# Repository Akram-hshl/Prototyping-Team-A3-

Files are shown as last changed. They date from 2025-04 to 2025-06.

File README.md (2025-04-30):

# Line Follower RC Car with Obstacle Detection

This project focuses on building a smart **line-following RC car** that autonomously navigates along a track while avoiding obstacles in its path. The car uses a combination of **ultrasonic sensors**, **IR sensors**, **servo motors**, and **motor drivers** to follow a designated line and actively detect and avoid obstacles.

## Key Components:
- **IR Sensors**: Used to detect the line and keep the car on track.
- **Ultrasonic Sensor**: Detects obstacles in the car's path, enabling it to avoid collisions.
- **Servo Motors**: Control the movement of the car, ensuring smooth navigation along the line.

### Goal:
The main objective of this project is to integrate these components into a cohesive system that not only follows the line but also reacts to its environment by avoiding obstacles. This makes the project a great introduction to robotics and autonomous systems.

---

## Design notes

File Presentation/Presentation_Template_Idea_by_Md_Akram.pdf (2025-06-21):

1. Introduction and Motivation -Md Akram
2. SysML diagram (requirement, use case and activity any one or two as your wish) -Jhon
3. SysML diagram (block, state machine, sequence any one or two as your wish) -Latif
4. 3D Design & Paper Sketch -Md Akram
5. Hardware requirement (Used Components list only) and Assembly process in details -Jhon
6. Thinker Cad Simulation video and Proteus layout diagram of components pins layout -Md Akram
7. Uppaal modeling, deadlock free verification and timed behavior -Latif (please include simulation

video)

8. Programing and Implementation
- Line Following (IR Sensor, motor driver and motor details and Used algorithm for our

system. If possible add a video as a proof it functional) -Jhon

- Obstacles Detection and avoidance (Ultrasonic Sensor and servo motor in details and

Used algorithm for our system. If possible add a video as a proof it functional) -Latif or

Md Akram any one

- Color Sensor Integration for Push, avoid and parking (Color sensor details and Used

algorithm for our system. If possible add a video as a proof it functional) -Latif or Md

Akram any one

9. Implementation overview and Statistics -Md Akram
10. Conclusion and future work - Jhon

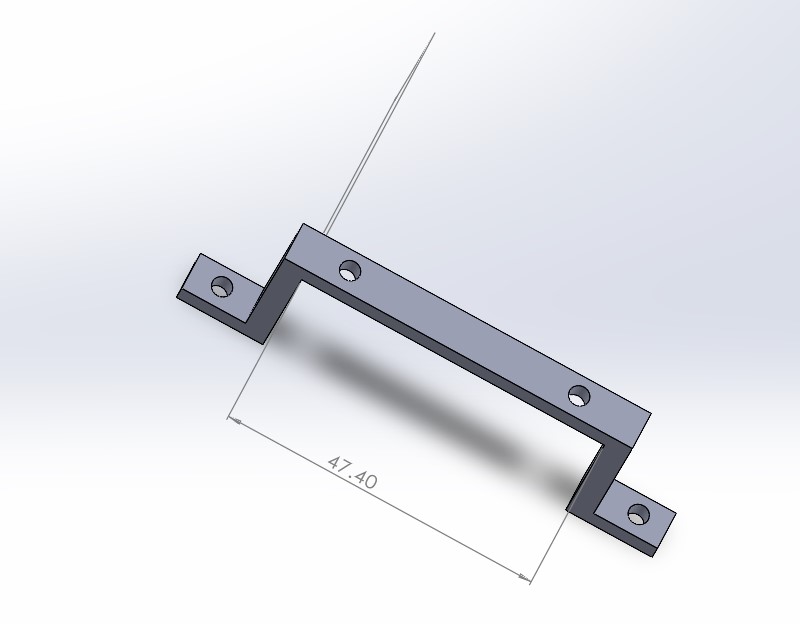
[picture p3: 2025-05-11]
Task 3 (Final Sysml, Switch case, Paper Sketch)/battery_holder.jpg

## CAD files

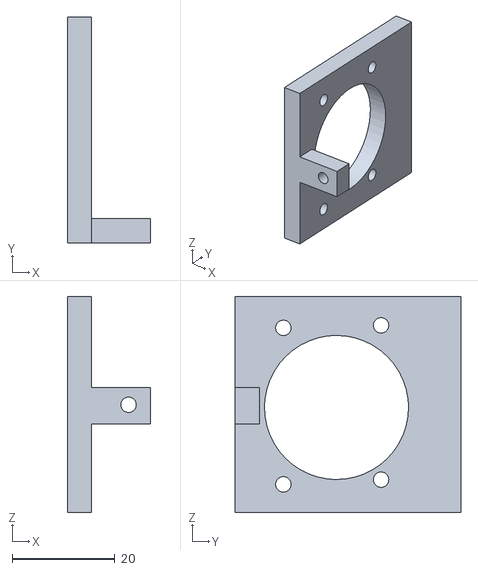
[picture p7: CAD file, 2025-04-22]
3D parts .stl format/P03_TA3_Colour_sensor_holder.STL
16.1 x 43.9 x 42.0

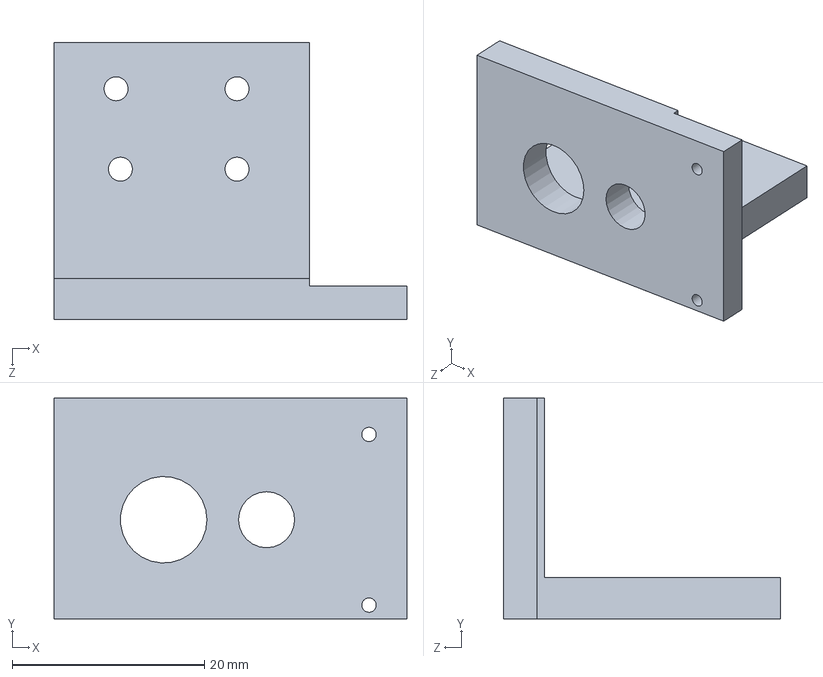
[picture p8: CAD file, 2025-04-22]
3D Parts/P05_TA3_Motor_holder_right.SLDPRT
36.7 x 23.0 x 28.8 mm

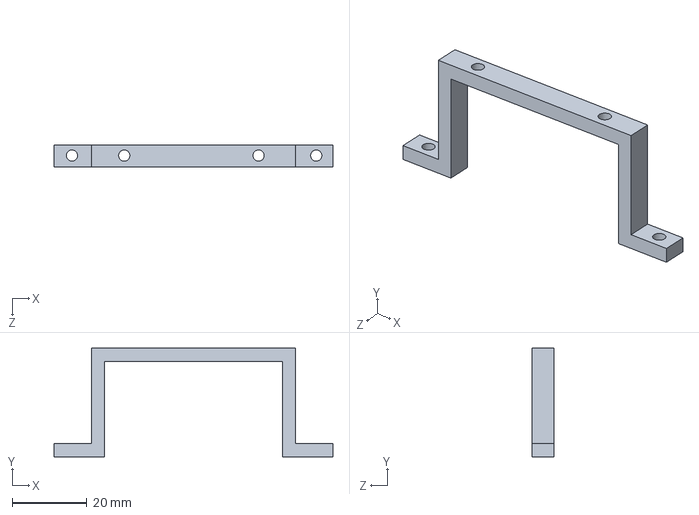
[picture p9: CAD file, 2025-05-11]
Task 3 (Final Sysml, Switch case, Paper Sketch)/P11_TA3_Battery_holder_backt side support.SLDPRT
74.5 x 29.1 x 6.00 mm

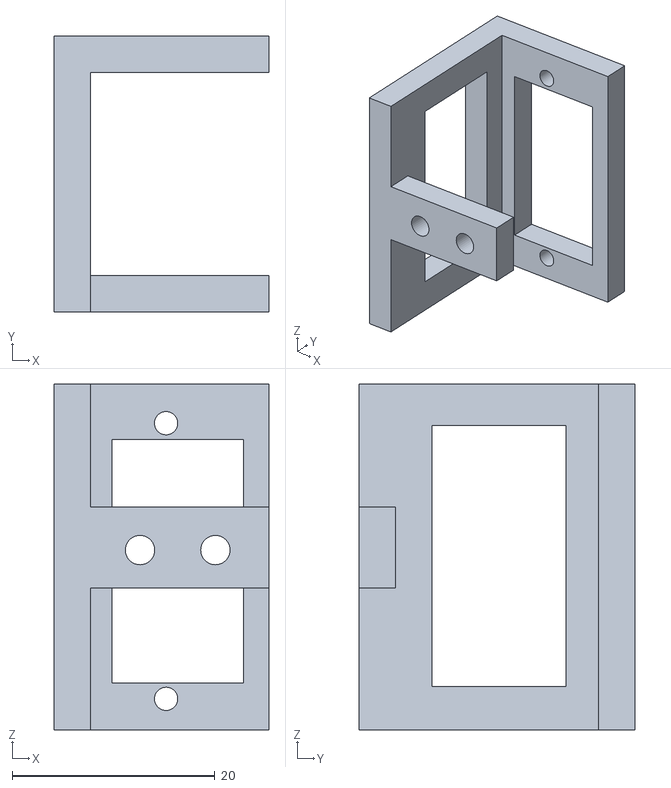
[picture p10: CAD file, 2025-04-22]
3D parts .stl format/P06_TA3_Servo_holder.STL
21.2 x 27.3 x 34.2

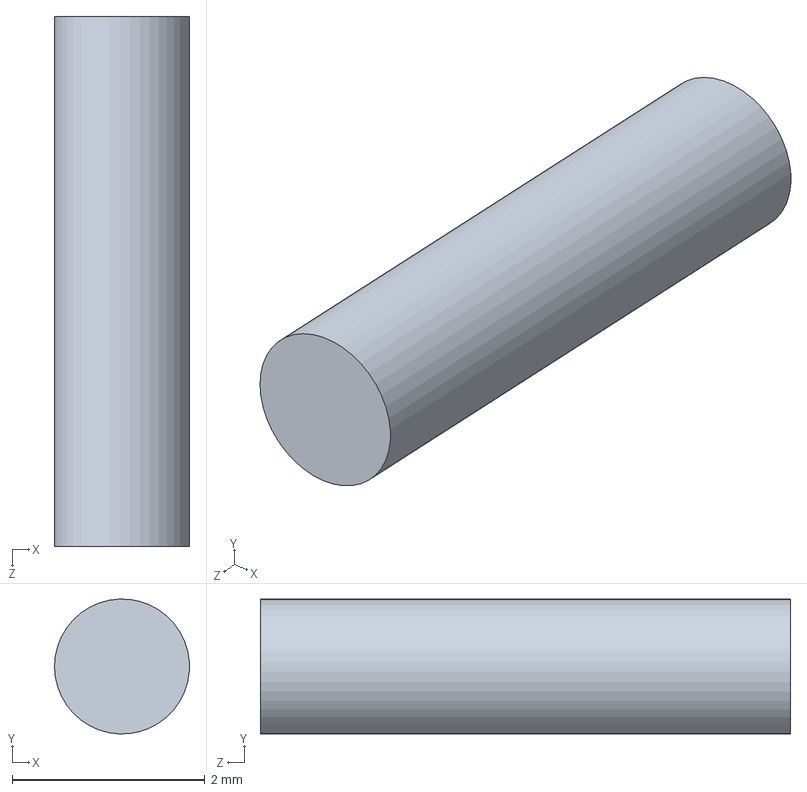
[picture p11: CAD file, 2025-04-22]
3D Parts/P08_TA3_Strick_Top.SLDPRT
1.40 x 1.40 x 5.50 mm

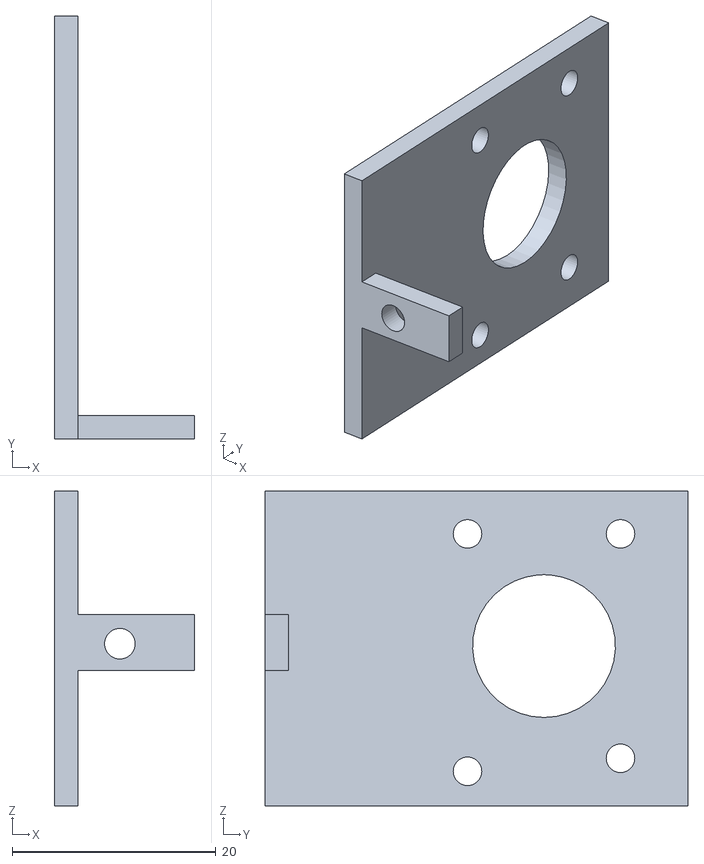
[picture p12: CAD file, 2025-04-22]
3D parts .stl format/P10_TA3_Extra_part_Pi_Camera_holder.STL
13.7 x 41.5 x 30.9

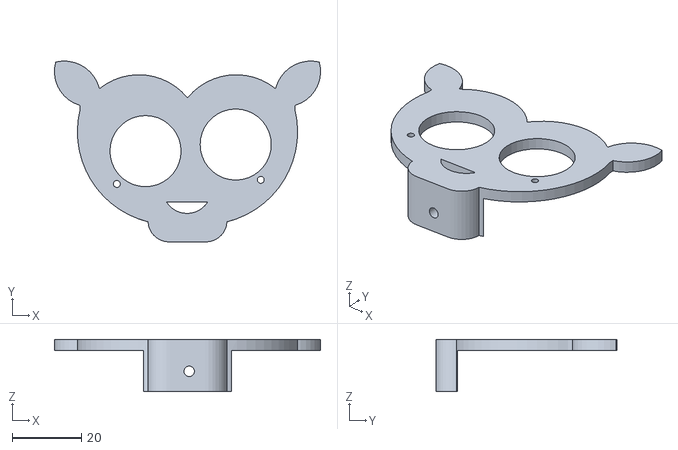
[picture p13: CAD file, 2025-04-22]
3D parts .stl format/P07_TA3_Ultrasonic_holder.STL
76.7 x 52.1 x 15.0

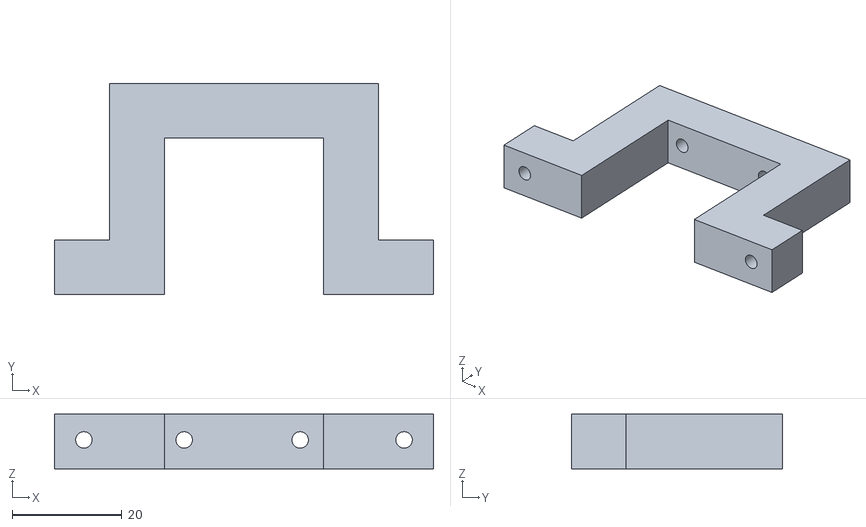
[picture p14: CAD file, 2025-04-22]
3D parts .stl format/P02_TA3_Battery_holder_front side support.STL
69.0 x 38.5 x 10.0

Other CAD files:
3D Parts/P10_TA3_Extra_part_Pi_Camera_holder.SLDPRT
3D Parts/P09_TA3_Strick_Bottom - Copy.SLDPRT
3D Parts/P07_TA3_Ultrasonic_holder.SLDPRT
3D parts .stl format/P08_TA3_Strick_Top.STL
3D Parts/P01_TA3_Battery_holder_backt side support.SLDPRT
3D parts .stl format/P05_TA3_Motor_holder_right.STL
3D Parts/P04_TA3_Motor_holder_left.SLDPRT
3D parts .stl format/P09_TA3_Strick_Bottom - Copy.STL
3D Parts/P06_TA3_Servo_holder.SLDPRT
3D parts .stl format/P04_TA3_Motor_holder_left.STL
3D Parts/P02_TA3_Battery_holder_front side support.SLDPRT
3D Parts/P03_TA3_Colour_sensor_holder.SLDPRT
3D parts .stl format/P01_TA3_Battery_holder_backt side support.STL

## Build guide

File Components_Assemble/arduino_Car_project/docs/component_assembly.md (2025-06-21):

# Component Assembly Log  
**Date:** May 11, 2025  
**Prepared by:** Onyesi John Abiagam  

## Overview  
This log records the physical setup and wiring of components for our robot during the prototyping stage. The focus was on connecting the motors, sensors, and power system properly before moving into software testing.

## Components Connected  

| Component | Connection Details |
|---|---|
| **DC Motors** | Connected to L298N motor driver: IN1–D6, IN2–D7, IN3–D8, IN4–D9. ENA on D10, ENB on D5. |
| **Ultrasonic Sensor (HC-SR04)** | Echo → A2, Trig → A3 |
| **IR Sensors (x2)** | Left sensor to A0, Right sensor to A1 |
| **Servo Motor** | Signal connected to D11, powered using external 5V |
| **Color Sensor (TCS3200)** | S0–S3 connected to D2–D5, OUT pin to D12 |
| **Power Supply** | 9V Li-ion battery to 5V voltage regulator, which powers the Arduino and sensors. All GNDs are linked. |

## What Was Done  
- All components were mounted on the chassis or breadboard.
- Double-checked wire connections for correct pins and voltage levels.
- Powered up the system and tested for signs of life (blinking LEDs, initial sensor response).
- Ran basic test code for IR sensors, ultrasonic sensor, servo, and motors to confirm they’re working.

## Notes  
- No visible signs of short circuits or heating.
- Servo works better when powered from the regulator, not directly from Arduino 5V.
- IR sensors responded correctly to black and white surfaces.
- Distance sensor gave expected readings (within ~2 cm error).
- Color sensor needs more lighting to give consistent results.

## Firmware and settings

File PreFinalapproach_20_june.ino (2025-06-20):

// Motor control pins for L298N
#define IN1 8
#define IN2 9
#define ENA 3

#define IN3 10
#define IN4 11
#define ENB 5
#define servo A5 // Servo motor control pin

// Line sensor pins
const int L_S = 2;
const int R_S = 4;

// Ultrasonic sensor pins
const int trigPin = 13;
const int echoPin = 12;

// Speed settings
const int RespeedL = 50;
const int RespeedR = 50;
const int speedL = 55;
const int speedR = 55;
const int speedLa = 75;
const int speedRa = 75;

// Obstacle detection
const int Set = 35;  

int distance_F = 0;

void setup() {
  pinMode(L_S, INPUT);
  pinMode(R_S, INPUT);

  pinMode(ENA, OUTPUT); pinMode(IN1, OUTPUT); pinMode(IN2, OUTPUT);
  pinMode(ENB, OUTPUT); pinMode(IN3, OUTPUT); pinMode(IN4, OUTPUT);

  pinMode(trigPin, OUTPUT);
  pinMode(echoPin, INPUT);
  pinMode(servo, OUTPUT);

  // Initialize servo to face forward
  servoPulse(servo, 70);
  Serial.begin(9600);
  delay(1000);
}

void loop() {
  distance_F = Ultrasonic_read();
  Serial.print("Distance Forward = ");
  Serial.print(distance_F);
  Serial.println(" cm");

  int leftSensor = digitalRead(L_S);
  int rightSensor = digitalRead(R_S);

  if ((rightSensor == 0) && (leftSensor == 0)) {
    if (distance_F > Set) {
      forward();
    } else {
      avoidObstacle();
    }
  } else if ((rightSensor == 1) && (leftSensor == 0)) {
    turnRight();
  } else if ((rightSensor == 0) && (leftSensor == 1)) {
    turnLeft();
  } else if ((rightSensor == 1) && (leftSensor == 1)) {

    Stop();
  }

  delay(10);
}
void avoidObstacle(){
  Stop();
  delay(300);
  aturnRight();
  delay(400);
  Stop();
  delay(400);
  aforward();
  delay(500);
  Stop();
  delay(200);
  aturnLeft();
  delay(400);
  Stop();
  delay(200);
  Reforward();
  delay(400);
}


int Ultrasonic_read() {
  digitalWrite(trigPin, LOW); 
  delayMicroseconds(2);
  digitalWrite(trigPin, HIGH); 
  delayMicroseconds(10);
  digitalWrite(trigPin, LOW);

  long duration = pulseIn(echoPin, HIGH, 30000);
  if (duration == 0) return 999;

  return duration / 29 / 2;
}
// Servo pulse function
void servoPulse(int pin, int angle) {
  int pwm = (angle * 11) + 500;
  digitalWrite(pin, HIGH);
  delayMicroseconds(pwm);
  digitalWrite(pin, LOW);
  delay(20);
}
// Movement functions
void forward() {
  analogWrite(ENA, speedL); analogWrite(ENB, speedR);
  digitalWrite(IN1, HIGH); digitalWrite(IN2, LOW);
  digitalWrite(IN3, HIGH); digitalWrite(IN4, LOW);
}
void Reforward() {
  analogWrite(ENA, RespeedL); analogWrite(ENB, RespeedR);
  digitalWrite(IN1, HIGH); digitalWrite(IN2, LOW);
  digitalWrite(IN3, HIGH); digitalWrite(IN4, LOW);
}
void aforward() {
  analogWrite(ENA, speedLa); analogWrite(ENB, speedRa);
  digitalWrite(IN1, HIGH); digitalWrite(IN2, LOW);
  digitalWrite(IN3, HIGH); digitalWrite(IN4, LOW);
}
void backward() {
  analogWrite(ENA, speedLa); analogWrite(ENB, speedRa);
  digitalWrite(IN1, LOW); digitalWrite(IN2, HIGH);
  digitalWrite(IN3, LOW); digitalWrite(IN4, HIGH);
}

void turnRight() {
  analogWrite(ENA, speedL); analogWrite(ENB, speedR);
  digitalWrite(IN1, LOW); digitalWrite(IN2, HIGH);
  digitalWrite(IN3, HIGH); digitalWrite(IN4, LOW);
}
void aturnRight() {
  analogWrite(ENA, speedLa); analogWrite(ENB, speedRa);
  digitalWrite(IN1, LOW); digitalWrite(IN2, HIGH);
  digitalWrite(IN3, HIGH); digitalWrite(IN4, LOW);
}

void turnLeft() {
  analogWrite(ENA, speedL); analogWrite(ENB, speedR);
  digitalWrite(IN1, HIGH); digitalWrite(IN2, LOW);
  digitalWrite(IN3, LOW); digitalWrite(IN4, HIGH);
}
void aturnLeft() {
  analogWrite(ENA, speedLa); analogWrite(ENB, speedRa);
  digitalWrite(IN1, HIGH); digitalWrite(IN2, LOW);
  digitalWrite(IN3, LOW); digitalWrite(IN4, HIGH);
}

void Stop() {
  analogWrite(ENA, 0); analogWrite(ENB, 0);
  digitalWrite(IN1, LOW); digitalWrite(IN2, LOW);
  digitalWrite(IN3, LOW); digitalWrite(IN4, LOW);
}

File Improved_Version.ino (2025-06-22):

const uint8_t speedLineLeft     = 55;
const uint8_t speedLineRight    = 50;
const uint8_t speedAlignLeft    = 75;
const uint8_t speedAlignRight   = 70;
const uint8_t speedPushLeft     = 120;
const uint8_t speedPushRight    = 120;

#define IN1 8
#define IN2 9
#define ENA 3
#define IN3 10
#define IN4 11
#define ENB 5

#define SERVO_PIN A5
const uint8_t lineSensorLeft    = 2;
const uint8_t lineSensorRight   = 4;

#define COLOR_SENSOR_OUT A0
#define COLOR_SENSOR_S0 A1
#define COLOR_SENSOR_S1 A2
#define COLOR_SENSOR_S2 A3
#define COLOR_SENSOR_S3 A4

const uint8_t obstacleThreshold = 5;
uint16_t distanceFront = 0;

void setup() {
  pinMode(L_S, INPUT);
  pinMode(R_S, INPUT);

  pinMode(ENA, OUTPUT); pinMode(IN1, OUTPUT); pinMode(IN2, OUTPUT);
  pinMode(ENB, OUTPUT); pinMode(IN3, OUTPUT); pinMode(IN4, OUTPUT);

  pinMode(trigPin, OUTPUT);
  pinMode(echoPin, INPUT);
  pinMode(servo, OUTPUT);
  pinMode(S0_PIN, OUTPUT);
  pinMode(S1_PIN, OUTPUT);
  pinMode(S2_PIN, OUTPUT);
  pinMode(S3_PIN, OUTPUT);
  pinMode(OUT_PIN, INPUT);

  digitalWrite(S0_PIN, HIGH);
  digitalWrite(S1_PIN, LOW);

  // Initialize servo to face forward
  servoPulse(servo, 70);
  Serial.begin(9600);
  delay(1000);
}

void loop() {
  distance_F = Ultrasonic_read();
  Serial.print("Distance Forward = ");
  Serial.print(distance_F);
  Serial.println(" cm");

  int leftSensor = digitalRead(L_S);
  int rightSensor = digitalRead(R_S);
  int sensorState = leftSensor * 2 + rightSensor;

  switch (sensorState) {
    case 0: // Both sensors on line
      if (distance_F > Set) {
        forward();
      } else {
        Stop();
        delay(1000);
        int color = getColor();
        switch (color) {
          case 1:
            avoidObstacle();  // Red
            break;
          case 2:
            push();           // Blue
            break;
          case 3:
            ParkCar();        // Green
            break;
          default:
            Stop();           // Unknown color
            break;
        }
      }
      break;

    case 1: // Left = 0, Right = 1 → turnRight
      turnRight();
      break;

    case 2: // Left = 1, Right = 0 → turnLeft
      turnLeft();
      break;

    case 3: // Both sensors off line
      Stop();
      break;
  }

  delay(10);
}

void avoidObstacle() {
  int distance_Left = 0;
  int distance_Right = 0;
  Stop();
  delay(500);

  for (int angle = 70; angle >= 0; angle -= 5) {
    servoPulse(servo, angle);
  }
  delay(500);
  distance_Right = Ultrasonic_read();
  Serial.print("Right Distance: ");
  Serial.println(distance_Right);
  delay(100);

  if (distance_Right > Set) {
    aturnRight(); delay(300); Stop(); delay(1000);
    for (int angle = 0; angle <= 70; angle += 5) {
      servoPulse(servo, angle);
    }
    aforward(); delay(800); Stop(); delay(1000);
    aturnLeft(); delay(300); Stop(); delay(300);
  } else {
    for (int angle = 70; angle <= 140; angle += 5) {
      servoPulse(servo, angle);
    }
    delay(500);
    distance_Left = Ultrasonic_read();
    Serial.print("Left Distance: ");
    Serial.println(distance_Left);
    delay(100);

    if (distance_Left > Set) {
      aturnLeft(); delay(300); Stop(); delay(1000);
      for (int angle = 140; angle >= 70; angle -= 5) {
        servoPulse(servo, angle);
      }
      aforward(); delay(600); Stop(); delay(1000);
      aturnRight(); delay(400); Stop(); delay(300);
    }
  }
}

int Ultrasonic_read() {
  digitalWrite(trigPin, LOW); 
  delayMicroseconds(2);
  digitalWrite(trigPin, HIGH); 
  delayMicroseconds(10);
  digitalWrite(trigPin, LOW);

  long duration = pulseIn(echoPin, HIGH, 30000);
  if (duration == 0) return 999;

  return duration / 29 / 2;
}

void servoPulse(int pin, int angle) {
  int pwm = (angle * 11) + 500;
  digitalWrite(pin, HIGH);
  delayMicroseconds(pwm);
  digitalWrite(pin, LOW);
  delay(20);
}

int getColor() {
  int redValue, greenValue, blueValue;

  // Red
  digitalWrite(S2_PIN, LOW);
  digitalWrite(S3_PIN, LOW);
  redValue = pulseIn(OUT_PIN, LOW);

  // Green
  digitalWrite(S2_PIN, HIGH);
  digitalWrite(S3_PIN, HIGH);
  greenValue = pulseIn(OUT_PIN, LOW);

  // Blue
  digitalWrite(S2_PIN, LOW);
  digitalWrite(S3_PIN, HIGH);
  blueValue = pulseIn(OUT_PIN, LOW);

  Serial.print("Red: ");
  Serial.print(redValue);
  Serial.print("\tGreen: ");
  Serial.print(greenValue);
  Serial.print("\tBlue: ");
  Serial.println(blueValue);

  int minValue = min(redValue, min(greenValue, blueValue));

  if (minValue == redValue) {
    return 1; // Red
  } else if (minValue == blueValue) {
    return 2; // Blue
  } else if (minValue == greenValue) {
    return 3; // Green
  } else {
    return 0;
  }
}

// Movement functions
void forward() {
  analogWrite(ENA, speedL); analogWrite(ENB, speedR);
  digitalWrite(IN1, HIGH); digitalWrite(IN2, LOW);
  digitalWrite(IN3, HIGH); digitalWrite(IN4, LOW);
}

void aforward() {
  analogWrite(ENA, speedLa); analogWrite(ENB, speedRa);
  digitalWrite(IN1, HIGH); digitalWrite(IN2, LOW);
  digitalWrite(IN3, HIGH); digitalWrite(IN4, LOW);
}

void pforward() {
  analogWrite(ENA, speedLp); analogWrite(ENB, speedRp);
  digitalWrite(IN1, HIGH); digitalWrite(IN2, LOW);
  digitalWrite(IN3, HIGH); digitalWrite(IN4, LOW);
}

void backward() {
  analogWrite(ENA, speedL); analogWrite(ENB, speedR);
  digitalWrite(IN1, LOW); digitalWrite(IN2, HIGH);
  digitalWrite(IN3, LOW); digitalWrite(IN4, HIGH);
}

void turnRight() {
  analogWrite(ENA, speedL); analogWrite(ENB, speedR);
  digitalWrite(IN1, LOW); digitalWrite(IN2, HIGH);
  digitalWrite(IN3, HIGH); digitalWrite(IN4, LOW);
}

void aturnRight() {
  analogWrite(ENA, speedLa); analogWrite(ENB, speedRa);
  digitalWrite(IN1, LOW); digitalWrite(IN2, HIGH);
  digitalWrite(IN3, HIGH); digitalWrite(IN4, LOW);
}

void turnLeft() {
  analogWrite(ENA, speedL); analogWrite(ENB, speedR);
  digitalWrite(IN1, HIGH); digitalWrite(IN2, LOW);
  digitalWrite(IN3, LOW); digitalWrite(IN4, HIGH);
}

void aturnLeft() {
  analogWrite(ENA, speedLa); analogWrite(ENB, speedRa);
  digitalWrite(IN1, HIGH); digitalWrite(IN2, LOW);
  digitalWrite(IN3, LOW); digitalWrite(IN4, HIGH);
}

void Stop() {
  analogWrite(ENA, 0); analogWrite(ENB, 0);
  digitalWrite(IN1, LOW); digitalWrite(IN2, LOW);
  digitalWrite(IN3, LOW); digitalWrite(IN4, LOW);
}

void push() {
  pforward(); delay(500);
  Stop(); delay(500);
}

void ParkCar() {
  aturnRight(); delay(300); Stop(); delay(1000);
  backward(); delay(5000);
}

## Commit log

2025-05-11 Add files via upload
    Corructed Battery holder
    [P11_TA3_Battery_holder_backt side support.SLDPRT]
2025-05-11 Add files via upload
    battery holder image
2025-05-11 Add files via upload
    Code with switch case
2025-05-11 Add files via upload
    Thinkerrcad simulution with swithch case formate
2025-06-07 Update imp.txt
    Dc motor and Ir sensor testing
2025-06-10 UPPAAL Modelling
    Missing the Color sensor template ( still ongoing )
2025-06-10 UPPAAL
    Missing the color sensor template ( still ongoing )
2025-06-21 Components assembly and tests
